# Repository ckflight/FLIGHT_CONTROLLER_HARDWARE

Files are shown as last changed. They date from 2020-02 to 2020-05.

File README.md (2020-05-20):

# FLIGHT_CONTROLLER_HARDWARE

This is the first Flight_Controller Board i designed a few years ago with Atmel SAM3X8E ARM Cortex M3, BNO055 Orientation Sensor, TPA2012D Audio Amplifier, CC2541 Bluetooth IC, 4 Channel PWM input for radio interface (no SBUS input is available on this version), Microcard Interface for data logging and ESC PWM pins. Board is tested on a Quadcopter and it is working fine.

CC2541 IC can be flashed with HM10 firmware for the simplicity if you do not want to implement your own 8051 code in it.

It can be used with Arduino IDE for simple test and implementation.

50 Ohm impedance microstrip transmission line is making 0.342mm trace width with below stackup.

2 x 1W Stereo Speaker can be connected to the Audio Amplifier.

Since this was my first flight controller board design, i did not added a good stand alone gyro sensor. Instead used BNO055 since it provides both Euler Angle and Gyroscope Accelerometer and Magnetometer results.

Stackup layer information can be found here: https://docs.oshpark.com/services/four-layer/



flight controller

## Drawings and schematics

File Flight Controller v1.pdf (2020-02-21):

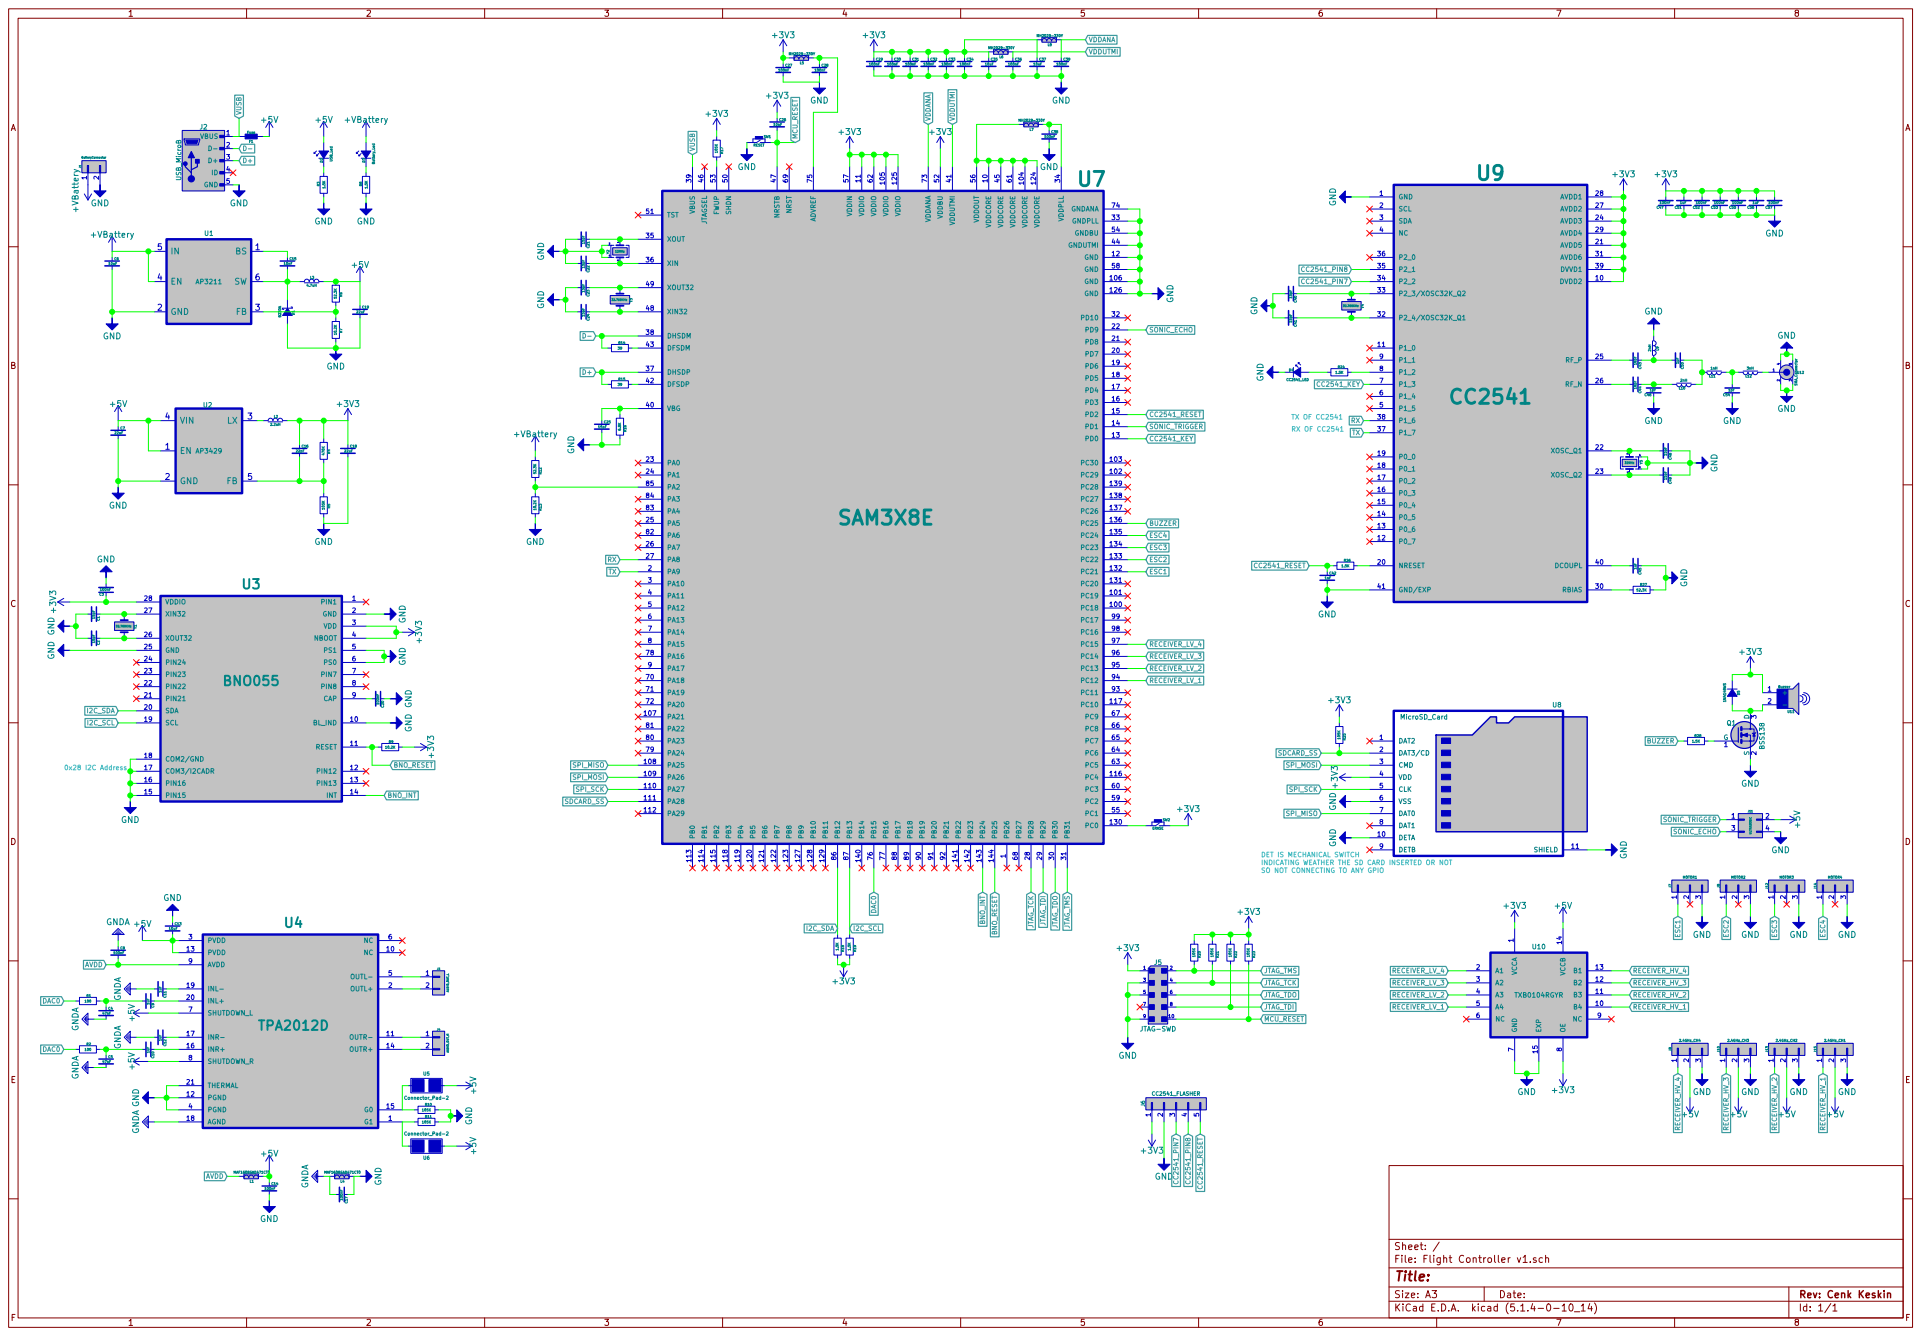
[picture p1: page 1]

1 VDDCORE 10 PC18 100 PC19 101 PC29 102 PC30 103 VDDCORE 104 VDDIO 105 GND 106 PA21 107 PA25 108 PA26 109 VDDIO 11 PA27 110 PA28 111 PA29 112 PB0 113 PB1 114 PB2 115 PC4 116 PC10 117 PB3 118 PB4 119 GND 12 PB5 120 PB6 121 PB7 122 PB8 123 VDDCORE 124 VDDIO 125 GND 126 PB9 127 PB10 128 PB11 129 PD0 13 PC0 130 PC20 131 PC21 132 PC22 133 PC23 134 PC24 135 PC25 136 PC26 137 PC27 138 PC28 139 PD1 14 PB14 140 PB22 141 PB23 142 PB24 143 PB25 144 PD2 15 PD3 16 PD4 17 PD5 18 PD6 19 PA9 2 PD7 20 PD8 21 PD9 22 PA0 23 PA1 24 PA5 25 PA7 26 PA8 27 PB28 28 PB29 29

8 NC 9 U10 TXB0104RGYR GNDGND GND +3V3 R23 105K R21 105K R22 105K R25 105K +3V3 DAT2 1 DETA 10 SHIELD 11 DAT3/CD 2 CMD 3 VDD 4 CLK 5 VSS 6 DAT0 7 DAT1 8 DETB 9 U8 MicroSD_Card

INDICATING WEATHER THE SD CARD INSERTED OR NOT SO NOT CONNECTING TO ANY GPIO

1 B4 10 B3 11 B2 12 B1 13 VCCB 14 EXP 15 A1 2 A2 3 A3 4 A4 5 NC 6 GND

File: Flight Controller v1.sch Sheet: /

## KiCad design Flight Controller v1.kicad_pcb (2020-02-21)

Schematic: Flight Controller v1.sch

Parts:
C1, C2, C21, C22, C23, C24, C25, C40, C41, C48, C49: 15pF; SMD_0402
C3, C8, C14, C17, C20, C27, C28, C29, C30, C31, C32, C33, C34, C36, C38, C39, C47, C52, C53, C55, C57: 100nF; SMD_0402
C4, C5: 47nF; SMD_0402
C6, C13, C35, C37: 10uF; SMD_0603
C7, C18, C19: 22uF; SMD_0805
C9, C10, C11, C12, C45, C51, C56: 1uF; SMD_0402
C15, C26: 10nF; SMD_0402
C16: 22pF; SMD_0402
C42: 1nF; SMD_0402
C43, C44: 18pF; SMD_0402
C46, C50, C54: 1pF; SMD_0402
D1: B230A; Diode_B230A
D2: USB_Led; Diode_0603
D3: Battery_Led; Diode_0603
D4: CC2541_LED; Diode_0603
D5: 1N4148WS; Diode_SOD-323
F1: Fuse; SMD_0603
J1: BatteryConnector; PinHeader_1x2-2.54mm
J2: USB_MicroB; USB_MicroB-TH
J3: AUDIO_OUT_L; PinHeader_1x2-2.54mm
J4: AUDIO_OUT_R; PinHeader_1x2-2.54mm
J5: JTAG-SWD
J6: CC2541_FLASHER; PinHeader_1x5-2.54mm
J7: MOTOR1; PinHeader_1x3-2.54mm
J8: 2.4GHz_CH4; PinHeader_1x3-2.54mm
J9: MOTOR2; PinHeader_1x3-2.54mm
J10: 2.4GHz_CH3; PinHeader_1x3-2.54mm
J11: ULTRASONIC; PinHeader_2x2-2.54mm
J12: MOTOR3; PinHeader_1x3-2.54mm
J13: 2.4GHz_CH2; PinHeader_1x3-2.54mm
J14: MOTOR4; PinHeader_1x3-2.54mm
J15: 2.4GHz_CH1; PinHeader_1x3-2.54mm
L1, L4: MAF1608GAD471CT0; SMD_0603
L2: 2.2uH; SMD_0805
L3: 4.7uH; SMD_1210
L5, L6, L7, L8: MH2029-330Y; SMD_0805
L9, L10: 2nH; SMD_0402
L11: 1nH; SMD_0402
L12: 3nH; SMD_0402
Q1: BSS138
R1, R2: 100; SMD_0402
R3, R8, R18, R19, R24, R26, R28: 1.5K; SMD_0402
R4: 470K; SMD_0402
R5, R10, R11, R17, R20, R21, R22, R23, R25: 105K; SMD_0402
R6, R12, R27: 52.3K; SMD_0402
R7, R9, R13: 10.2K; SMD_0402
R14, R15: 39; SMD_0402
R16: 6.8K; SMD_0402
SW1: RESET; Button_B3U-1000P
SW2: ERASE; Button_B3U-1000P
U1: AP3211; SOT23-6
U2: AP3429; SOT23-5
U3: BNO055; LGA-28_4x5mm-Pitch0.5mm
U4: TPA2012D; QFN20-1EXP_4x4mm-Pitch0.5mm
U5, U6: Connector_Pad-2
U7: SAM3X8E; LQFP-144_20x20mm-Pitch0.5mm
U8: MicroSD_Card; MicroSD_DM3AT-SF-PEJM5
U9: CC2541; QFN40-1EXP_6x6mm-Pitch0.5mm
U10: TXB0104RGYR; VQFN14-1EXP_4x4mm-Pitch0.5mm
U11: Buzzer; Buzzer_CSS-057SA
U12: SMA_Connector
Y1, Y3, Y4: 32.768KHz; ABS05_32.768KHz
Y2: 12MHz; Crystal_3.2mm-2.5mm
Y5: 32MHz; Crystal_2mm-1.6mm

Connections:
+3V3: C3.1, C16.1, C18.1, C26.1, C27.1, C29.1, C30.1, C31.1, C32.1, C33.1, C34.1, C35.1, C37.1, C47.2, C51.2, C52.2, C53.2, C55.2, C56.2, C57.2, D5.1 (K), J5.1, J6.1, L2.2, L5.1, L6.1, L8.1, R4.1, R9.2, R17.1, R18.2, R19.2, R20.1, R21.1, R22.1, R23.1, R25.1, SW2.2, U3.3 (VDD), U3.4 (NBOOT), U3.28 (VDDIO), U7.11 (VDDIO), U7.52 (VDDBU), U7.57 (VDDIN), U7.62 (VDDIO), U7.105 (VDDIO), U7.125 (VDDIO), U8.4 (VDD), U9.10 (DVDD2), U9.21 (AVDD5), U9.24 (AVDD3), U9.27 (AVDD2), U9.28 (AVDD1), U9.29 (AVDD4), U9.31 (AVDD6), U9.39 (DVVD1), U10.1 (VCCA), U10.8 (OE), U11.1 (+); also elsewhere on the board
+5V: C7.1, C13.2, C14.1, C19.1, D2.2 (A), F1.2, J8.2, J10.2, J11.2, J13.2, J15.2, L1.2, L3.2, R6.1, U2.1 (EN), U2.4 (VIN), U4.3 (PVDD), U4.7 (SHUTDOWN_L), U4.8 (SHUTDOWN_R), U4.13 (PVDD), U5.1, U6.2, U10.14 (VCCB); also elsewhere on the board
+VBattery: C6.1, D3.2 (A), J1.1, R12.1, U1.4 (EN), U1.5 (IN); also elsewhere on the board
AVDD: C8.2, L1.1, U4.9 (AVDD)
BNO_INT: U3.14 (INT), U7.143 (PB24)
BNO_RESET: R9.1, U3.11 (RESET), U7.144 (PB25)
BUZZER: R28.1, U7.136 (PC25)
CC2541_KEY: U7.13 (PD0), U9.7 (P1_3)
CC2541_PIN7: J6.3, U9.34 (P2_2)
CC2541_PIN8: J6.4, U9.35 (P2_1)
CC2541_RESET: C42.1, J6.5, R26.1, U7.15 (PD2)
D+: J2.3 (D+), R15.1, U7.37 (DHSDP)
D-: J2.2 (D-), R14.1, U7.38 (DHSDM)
DAC0: R1.1, R2.1, U7.76 (PB15)
ESC1: J7.1, U7.132 (PC21)
ESC2: J9.1, U7.133 (PC22)
ESC3: J12.1, U7.134 (PC23)
ESC4: J14.1, U7.135 (PC24)
GND: C1.2, C2.2, C3.2, C6.2, C7.2, C13.1, C14.2, C17.1, C18.2, C19.2, C20.1, C21.2, C22.2, C23.2, C24.2, C25.2, C27.2, C28.2, C29.2, C30.2, C31.2, C32.2, C33.2, C34.2, C35.2, C36.2, C37.2, C38.2, C39.2, C40.2, C41.2, C42.2, C45.1, C46.1, C47.1, C48.1, C49.1, C51.1, C52.1, C53.1, C54.1, C55.1, C56.1, C57.1, D1.2 (A), D4.1 (K), J1.2, J2.5 (GND), J5.3, J5.5, J5.9, J6.2, J7.3, J8.3, J9.3, J10.3, J11.4, J12.3, J13.3, J14.3, J15.3, L4.2, L9.1, Q1.2 (S), R3.1, R5.2, R7.2, R8.1, R10.2, R11.2, R13.2, R16.2, R27.2, SW1.1, U1.2 (GND), U2.2 (GND), U3.2 (GND), U3.5 (PS1), U3.6 (PS0), U3.10 (BL_IND), U3.15 (PIN15), U3.16 (PIN16), U3.17 (COM3/I2CADR), U3.18 (COM2/GND), U3.25 (GND), U4.4 (PGND), U4.12 (PGND), U4.21 (THERMAL), U7.12 (GND), U7.33 (GNDPLL), U7.44 (GNDUTMI), U7.54 (GNDBU), U7.58 (GND), U7.74 (GNDANA), U7.106 (GND), U7.126 (GND), U8.6 (VSS), U8.10 (DETA), U8.11 (SHIELD), U9.1 (GND), U9.41 (GND/EXP), U10.7 (GND), U10.15 (EXP), U12.2, U12.3, U12.4, U12.5, Y2.2, Y2.4, Y5.2, Y5.4; also elsewhere on the board
GNDA: C4.2, C5.2, C8.1, C11.2, C12.2, C17.2, L4.1, U4.18 (AGND)
I2C_SCL: R19.1, U3.19 (SCL), U7.87 (PB13)
I2C_SDA: R18.1, U3.20 (SDA), U7.86 (PB12)
JTAG_TCK: J5.4, R21.2, U7.28 (PB28)
JTAG_TDI: J5.8, R22.2, U7.29 (PB29)
JTAG_TDO: J5.6, U7.30 (PB30)
JTAG_TMS: J5.2, R20.2, U7.31 (PB31)
MCU_RESET: C26.2, J5.10, R23.2, SW1.2, U7.47 (NRSTB); also elsewhere on the board
unnamed: C1.1, U3.27 (XIN32), Y1.1
unnamed: C2.1, U3.26 (XOUT32), Y1.2
unnamed: C4.1, C9.2, R1.2
unnamed: C9.1, U4.20 (INL+)
unnamed: C10.1, U4.16 (INR+)
unnamed: C5.1, C10.2, R2.2
unnamed: C11.1, U4.19 (INL-)
unnamed: C12.1, U4.17 (INR-)
unnamed: C15.1, U1.1 (BS)
unnamed: C15.2, D1.1 (K), L3.1, U1.6 (SW)
unnamed: C16.2, R4.2, R5.1, U2.5 (FB)
unnamed: C20.2, U3.9 (CAP)
unnamed: C21.1, U7.35 (XOUT), Y2.1
unnamed: C22.1, U7.36 (XIN), Y2.3
unnamed: C23.1, U7.49 (XOUT32), Y3.1
unnamed: C24.1, U7.48 (XIN32), Y3.2
unnamed: C25.1, R16.1, U7.40 (VBG)
unnamed: C28.1, L5.2, U7.75 (ADVREF)
unnamed: C38.1, L7.2, U7.34 (VDDPLL)
unnamed: C40.1, U9.33 (P2_3/XOSC32K_Q2), Y4.1
unnamed: C41.1, U9.32 (P2_4/XOSC32K_Q1), Y4.2
unnamed: C43.1, C50.2, L9.2
unnamed: C43.2, U9.25 (RF_P)
unnamed: C44.1, C46.2, L10.2
unnamed: C44.2, U9.26 (RF_N)
unnamed: C45.2, U9.40 (DCOUPL)
unnamed: C48.2, U9.22 (XOSC_Q1), Y5.3
unnamed: C49.2, U9.23 (XOSC_Q2), Y5.1
unnamed: C50.1, L10.1, L11.2
unnamed: C54.2, L11.1, L12.2
unnamed 57: D2.1 (K), R3.2; also elsewhere on the board
unnamed 58: D3.1 (K), R8.2; also elsewhere on the board
unnamed 59: D4.2 (A), R24.1; also elsewhere on the board
unnamed: D5.2 (A), Q1.3 (D), U11.2 (-)
unnamed: J3.1, U4.5 (OUTL-)
unnamed: J3.2, U4.2 (OUTL+)
unnamed: J4.1, U4.11 (OUTR-)
unnamed: J4.2, U4.14 (OUTR+)
unnamed: L2.1, U2.3 (LX)
unnamed: L7.1, U7.10 (VDDCORE), U7.45 (VDDCORE), U7.56 (VDDOUT), U7.61 (VDDCORE), U7.104 (VDDCORE), U7.124 (VDDCORE)
unnamed: L12.1, U12.1
unnamed: Q1.1 (G), R28.2
unnamed: R6.2, R7.1, U1.3 (FB)
unnamed: R10.1, U4.15 (G0), U5.2
unnamed: R11.1, U4.1 (G1), U6.1
unnamed: R12.2, R13.1, U7.85 (PA2)
unnamed: R14.2, U7.43 (DFSDM)
unnamed: R15.2, U7.42 (DFSDP)
unnamed: R17.2, U7.53 (FWUP)
unnamed: R24.2, U9.8 (P1_2)
unnamed: R26.2, U9.20 (NRESET)
unnamed: R27.1, U9.30 (RBIAS)
unnamed 85: SW2.1, U7.130 (PC0); also elsewhere on the board
RECEIVER_HV_1: J15.1, U10.10 (B4)
RECEIVER_HV_2: J13.1, U10.11 (B3)
RECEIVER_HV_3: J10.1, U10.12 (B2)
RECEIVER_HV_4: J8.1, U10.13 (B1)
RECEIVER_LV_1: U7.94 (PC12), U10.5 (A4)
RECEIVER_LV_2: U7.95 (PC13), U10.4 (A3)
RECEIVER_LV_3: U7.96 (PC14), U10.3 (A2)
RECEIVER_LV_4: U7.97 (PC15), U10.2 (A1)
RX: U7.27 (PA8), U9.38 (P1_6)
SDCARD_SS: R25.2, U7.111 (PA28), U8.2 (DAT3/CD)
SONIC_ECHO: J11.3, U7.22 (PD9)
SONIC_TRIGGER: J11.1, U7.14 (PD1)
SPI_MISO: U7.108 (PA25), U8.7 (DAT0)
SPI_MOSI: U7.109 (PA26), U8.3 (CMD)
SPI_SCK: U7.110 (PA27), U8.5 (CLK)
TX: U7.2 (PA9), U9.37 (P1_7)
VDDANA: C39.1, L8.2, U7.73 (VDDANA)
VDDUTMI: C36.1, L6.2, U7.41 (VDDUTMI)
VUSB: F1.1, J2.1 (VBUS), U7.39 (VBUS)

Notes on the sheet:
0x28 I2C Address
TX OF CC2541
RX OF CC2541
DET IS MECHANICAL SWITCH INDICATING WEATHER THE SD CARD INSERTED OR NOT SO NOT CONNECTING TO ANY GPIO

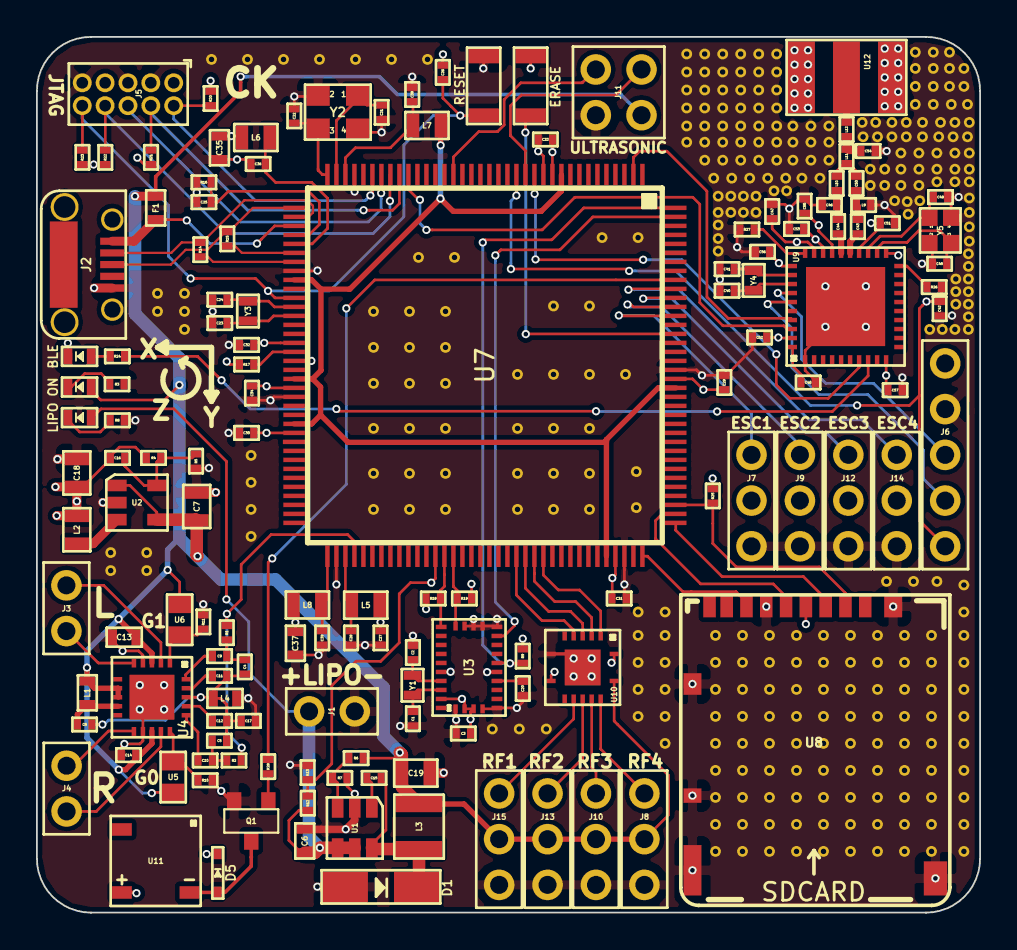
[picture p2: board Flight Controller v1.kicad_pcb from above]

Board: 4 copper layers, 52.4 x 48.7 mm, 138 parts (0 on the bottom side), 99 nets.

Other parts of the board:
BLE: CC2541_LED; Diode_0603
ERASE: ERASE; Button_B3U-1000P
LIPO: Battery_Led; Diode_0603
ON: USB_Led; Diode_0603
RESET: RESET; Button_B3U-1000P

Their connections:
+3V3: ERASE.2; also elsewhere on the board
+5V: ON.2; also elsewhere on the board
+VBattery: LIPO.2; also elsewhere on the board
GND: BLE.1, RESET.1; also elsewhere on the board
MCU_RESET: RESET.2; also elsewhere on the board
unnamed 57: ON.1; also elsewhere on the board
unnamed 58: LIPO.1; also elsewhere on the board
unnamed 59: BLE.2; also elsewhere on the board
unnamed 85: ERASE.1; also elsewhere on the board
